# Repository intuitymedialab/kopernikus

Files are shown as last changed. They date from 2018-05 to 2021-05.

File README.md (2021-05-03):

# Kopernikus Documentation

*an experimental prototyping platform to test and evaluate the vision of home robotics*

Developed at Intuity Media Lab GmbH in Stuttgart, Germany.

Kopernikus Total

## 🤔 Wait, what?

For a high level overview of the project, visit [https://kopernikus.intuity.de/](https://kopernikus.intuity.de/).

## 🔬 What this is about

Kopernikus is a small robot, that will cost less than EUR 1000 to build. If you put it together, you will have something like a remote control car, equipped with a quad core computer, a stereo camera, audio input and output and a video projector.
You'll be able to use it as a basic setup and build your personal project on top.

## 📓 A little backstory

The vision of home robotics is ubiquitous. As a transdisciplinary team of designers, technologists and researchers, we were looking for a way to prototype the concepts we've been working on.

The question becomes: how do you design AI? How can we build behavioural interfaces? One common example is robot navigation.

We want future robots to navigate through our apartments savely, in a manner that is understandable and predictable for humans. We want them to deal gracefully with unexpected obstacles and be efficient and save. 

One of our key interests is Heuristic Problem Solving, which uses concepts from cognitive science to implement a decision process similar to that of humans (You can read up on HPS <a href="https://easychair.org/publications/open/z2d">here</a>, a Paper by our team member Alexandra Kirsch). Our goal is to use HPS as a general, cognitively inspired decision-making framework and use Kopernikus as a use case and testing environment to gain insights through practical experiences. 

That's why Kopernikus is an experimental prototyping platform to test and evaluate the vision of home robotics.

## 💪 What you will be able to do

Fully loaded, Kopernikus offers the following hardware capabilities:

* 3D imaging
* mobile projection mapping (up to a certain extent)
* 3 channel audio input (good for locating sound sources)
* audio playback
* mobile, untethered use for about an hour(...ish - depends on your use)

## 🎒 What you will need

**Quick disclaimer:** *One of our main goals was to build Kopernikus as both low-budget and easy-to-use as possible. At some points compromises had to be made in order to a) stay in a reasonable budget or b) make it easy to assemble and use.*

All of the components can be bought online on Amazon, eBay, Banggood, Mouser etc. - prices might vary.

This is just a rough rundown of what key components were used so you get the idea. Check out the [parts list](Hardware/partsList.md) for a more detailled list with links.

#### 💻 Computing
* UpBoard
* Arduino Uno

#### 👀 Input
* RealSense R200
* USB Microphones
* RC Receiver

#### 🐸 Output
* RD02 Robotic Drive System
* Servo Motor
* Anker Soundcore
* USB soundcard
* PicoPro Projector

#### ⚡️ Power
* Laptop Powerbank

### Custom Parts

In order to hold everything together we went with a round base plate (in size similar to vacuum cleaning robots) with some mounting holes in a grid and 3D printed parts made from PLA. We used an Ultimaker 3 - which means, you can basically print them on any basic FDM printer.

Most parts were designed with quite broad tolerances so you shouldn't have that big of a problem to make it all fit together nicely.

The shielding for the projector out of acrylic glass is optional - its mainly meant to protect the projector from dust and physical damage (and because we liked the look to be honest 😎). We will upload a 3D file without the mounts for it later.

## Getting started

For getting started head over to the specific readmes on [Software](Software/README.md) and [Hardware](Hardware/README.md).

## TODO

* [x] Prepare 3D files for milling
* [ ] Create schematic
* [x] Create 3D files for milling

## License

This project is released under the MIT License - you are free to do whatever you want with it - as long as you don't plan on subdueing humanity or any other crazy stuff, we're fine with it.

You are not legally bound to it, but it would be nice if you credit this project when creating something with it - and please **tell us**! We would love to see what you create!

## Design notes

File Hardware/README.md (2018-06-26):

# Kopernikus Software Documentation

*an experimental prototyping platform to test and evaluate the vision of home robotics*

Developed at Intuity Media Lab GmbH in Stuttgart, Germany.

## Overview

Let's divide this up into ~~two~~ three parts:
1) Parts list
2) Assembly
3) Connecting everything

## 🛠 Fabrication

As mentioned before, all parts can be either 3D-printed or produced on a laser cutter / CNC mill.

### 3D printed parts

The parts were printed on an Ultimaker 3 in our office, but any FDM printer should produce similar results.
The models were created for printing them directly onto the build plate with as little support as possible to create one even reference surface.
The layer height was 0.1mm on finer objects and 0.3mm on the rough stuff.

### Machined parts

We used 5mm PVC for our base plate and the controller plate. We wouldnt recommend going a lot thinner, but 4mm should be fine too.
Using acrylic glass instead of PVC shouldn't be a problem either, we just had it laying around already.

---

⚠️ **Especially when using a laser cutter, stay away from PVC since it creates toxic fumes when cut!** ⚠️

---

## 🔌 Connect all the things!

Refer to [this](components/basic_electronic_connections.pdf?raw=true) plan on how to connect everything. Fitting all wires into the plan would probably have been to big and unnecessary - it's actually quite simple.

The pin mappings on the Arduino are:

```
Pin mappings Arduino:

RC_CH1_INPUT     - >    5
RC_CH2_INPUT     - >    6
RC_CH3_INPUT     - >    7
RC_CH4_INPUT     - >    4 
SERVO PIN        - >   11
RX               - >   10
TX               - >    9
```

### Power

Basically everything runs off a notebook powerbank that has all the charging and protection features already built in - so no working on risky LiPo battery packs is required here.

The battery pack can deliver up to 50W peak which is more than enough for our use. One issue we had from time to time though was that the battery pack has a protection built in that shuts off the power when too little current is drawn. This totally makes sense when using it for its intended purpose (which we don't).

#### Adding a power resistor
At some point this problem somehow vanished, but one possible solution would be adding a **power resistor** that draws a fixed base current and thus circumvents the automatic shutdown. It also increases the power draw in general, but it's probably the simplest solution.

We still need to check what value would be a good match though. Open to suggestions.

#### Basic power scheme

We created two independent circuits so you can control which devices are powered to save some battery life.

1) Arduino, RC receiver, motors, servo
2) UpBoard and its peripherals (like the 3D camera, microphones etc.)

Ready-made devices like the speaker, the projector etc. get their juice directly via USB and all have a power switch themselves.

#### Powering the UpBoard

The UpBoard uses a simple DC jack, but **behold**!
Usually these are used for 9V and 12V which **you should never at any time** feed into the UpBoard. 

**! The UpBoard takes 5V MAXIMUM !**

Eventhough the powerbank has a 5V output, it can't deliver enough current for the UpBoard to boot properly. Thus we used a cheap step down buck converter, capable of delivering up to 12 A (not the small LM2596 ones), set to 5V.

We also added a decoupling capacitor across the 5V and GND rails on the board - not sure if it's necessary after all.

#### Powering the motors

This is pretty straight-forward: The motor drivers need 12V to work, so you can just connect them directly to the battery pack.

#### Powering the Arduino (and peripherals)

The Arduino gets its power from the MD25 Board's integrated voltage regulator. It's powerful enough to power the Arduino and the RC receiver, but peripherals like the Servo need their own supply (in form of a 5V 1A Step-Down Module)

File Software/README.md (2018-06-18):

# Kopernikus Software Documentation

*an experimental prototyping platform to test and evaluate the vision of home robotics*

Developed at Intuity Media Lab GmbH in Stuttgart, Germany.

## Overview

There are two software packages needed
1) Arduino
2) UpBoard

## 🤖 Arduino Code

The Arduino is used for everything hardware related. This includes:
* Controlling the motors and reading their encoder values
* Receiving RC commands
* Controlling the servo
* Talking to the UpBoard via a serial protocol

### Libraries

We rely on some libraries that you will need to install prior to flashing the Arduino:
* ServoTimer2
* CommandHandler
-> 
* EnableInterrupt
-> [GitHub Repo](https://github.com/GreyGnome/EnableInterrupt)
* AltSoftSerial

They are all available through the Libary Manager included in the Arduino IDE.

### Flashing the Arduino

Getting the Arduino ready should be pretty straight-forward:

1) Download the [Arduino IDE](https://www.arduino.cc/en/Main/Software)
2) Download our files
3) Install the necessary libraries
4) Choose the appropriate board settings
5) Upload 🚀

## 💻 UpBoard

The UpBoard is a x86 based single board computer, so we are able to run a fully-fledged Ubuntu distro on it and thus write code in all kinds of environments.

### Setup

Getting the UpBoard set up properly might be a bit finicky or at least different when you come from a background mainly working with Raspberry Pis. Some packages and kernel versions are not compatible with the latest Ubuntu so better stick with [Ubuntu 16.04 (Xenial Xerus)](http://releases.ubuntu.com/16.04/).

Also make sure you [install the kernel updates](https://wiki.up-community.org/Ubuntu#Install_Ubuntu_kernel_for_UP_from_PPA) for the board afterwards!

### Software packages

#### Ubuntu Software Packages

These packages can be installed via *apt* using the following commands:

```
sudo apt-get install "package name"

// so something like this:

sudo apt-get install git
```
* git, gitk, git-gui (Git)
* mplayer (Media Player)
* audacity (Audacity for recording sound)
* default-jre (Java)

The main software responsible for decision making is written in Clojure. Head over to the specific readMe for further documentation.

#### Camera

The camera supports ROS as the main interface. Therefore we use ROS to connect the camera to Clojure. It would be possible also to run the serial connection to the base over ROS, but since ROS can be such a pain, it seems better to use it only when necessary.

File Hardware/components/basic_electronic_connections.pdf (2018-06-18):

## microphones

12 V

kopernikus | // basic electronic connections

the arduino gets its
power from the voltage
regulator in the md25

the usb hub is mainly used for charging compatible devices like the bluetooth speaker eventough it has its own battery already.

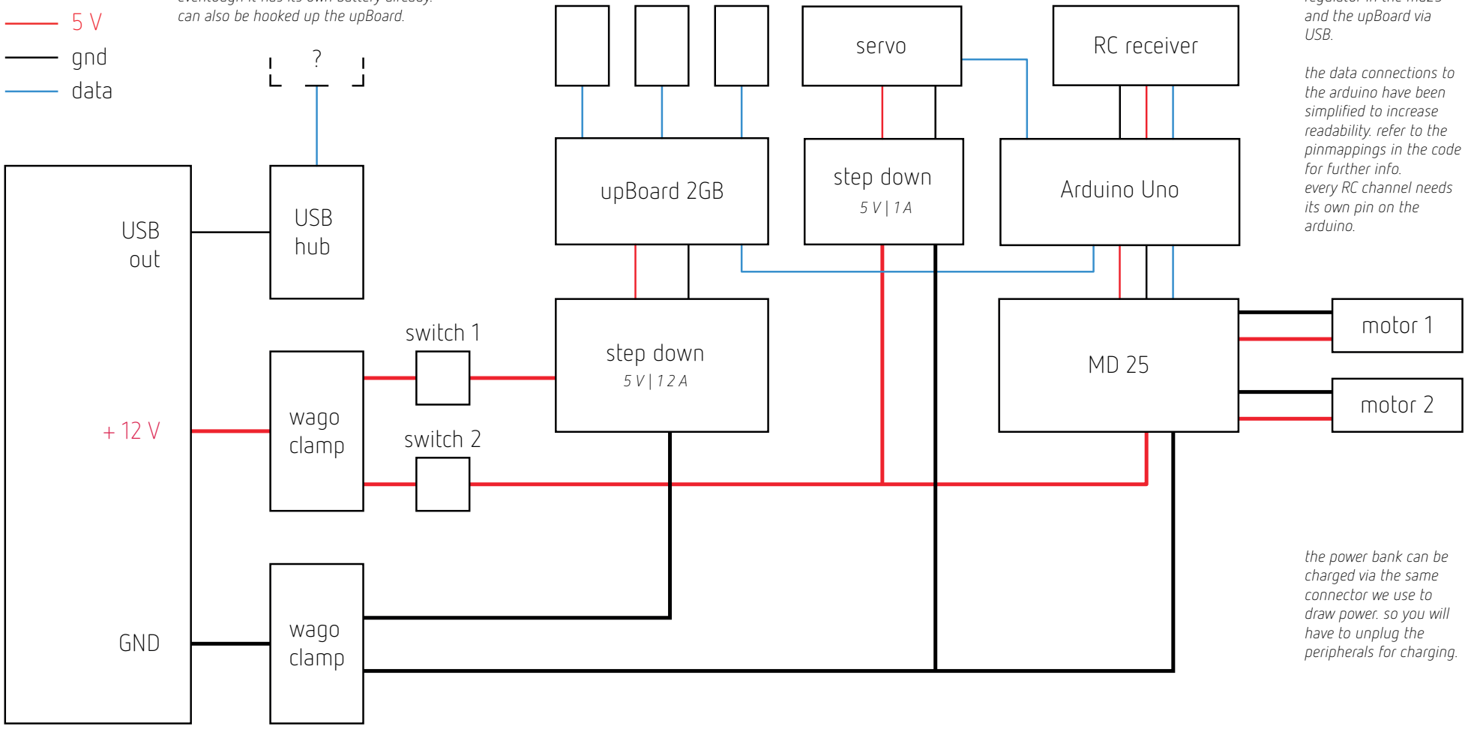
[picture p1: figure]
Arduino Uno; motor 1; motor 2; servo; RC receiver; step down 5 V | 1 A upBoard 2GB; step down; wago clamp; USB hub; 5 V gnd data; wago clamp GND; USB out; switch 1; switch 2; and the upBoard via USB.; the data connections to the arduino have been simplified to increase readability. refer to the pinmappings in the code for further info. every RC channel needs its own pin on the arduino.; the power bank can be charged via the same connector we use to draw power. so you will have to unplug the peripherals for charging.; can also be hooked up the upBoard. ?

intuity.de | aaiirr.net | kopernikus.bot | ⁄ª

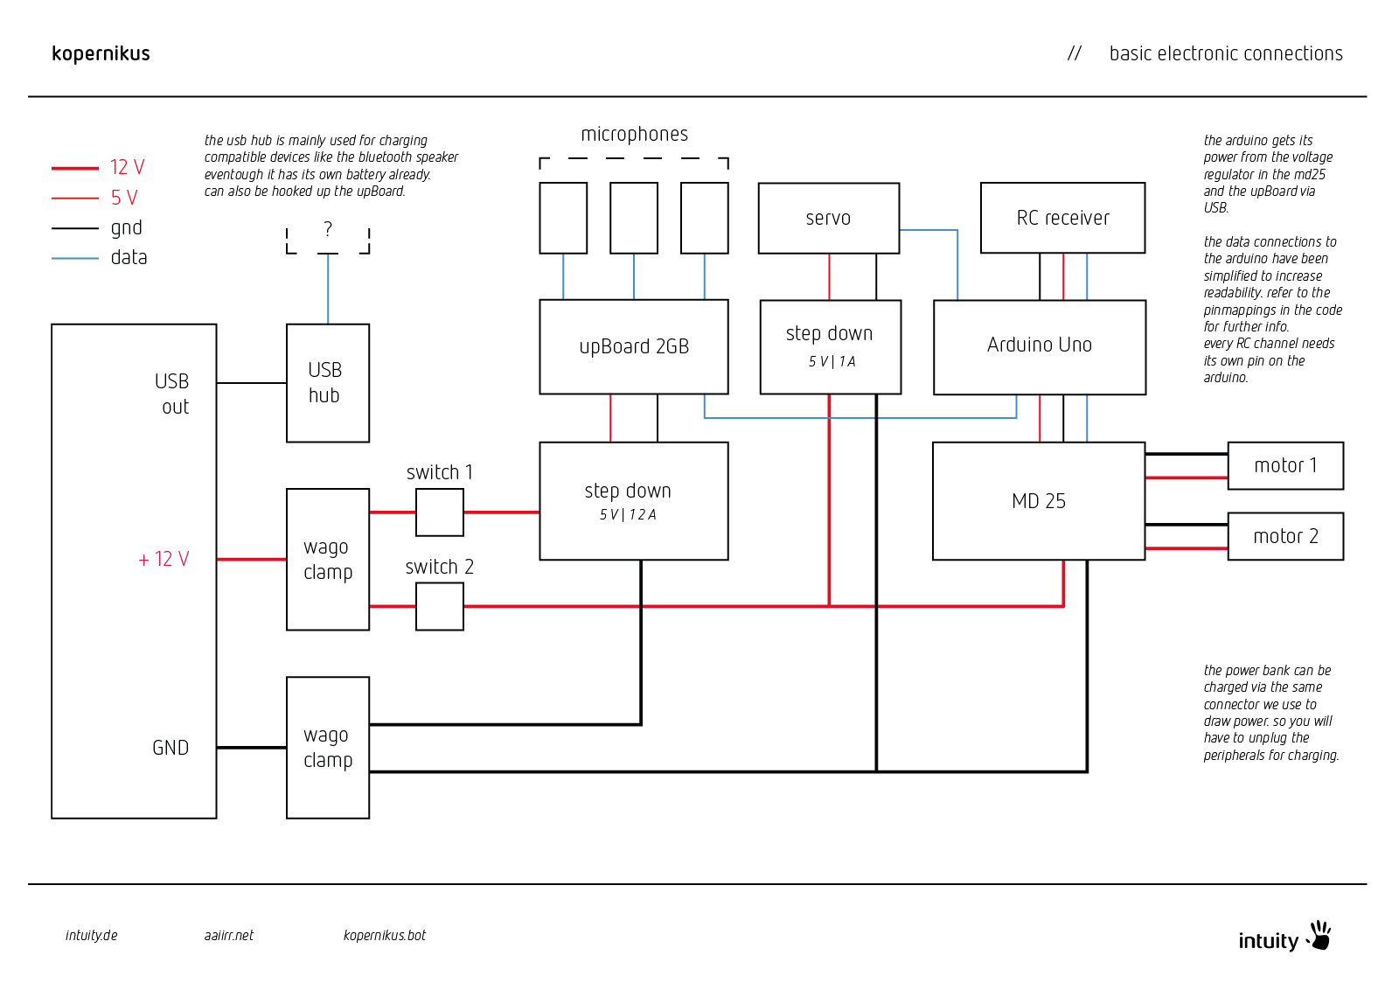
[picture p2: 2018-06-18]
Hardware/components/basic_electronic_connections.png

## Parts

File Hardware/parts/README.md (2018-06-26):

# Custom Parts

The 3D models were created with [Rhino 3D](https://www.rhino3d.com) - a commercial NURBS modelling software.

We uploaded both the NURBS and mesh-based models of Kopernikus, so you will be able to work with it.

## Download

-> NURBS (3dm format, zipped)

-> MESH (stl format, zipped)

## 3D Printing | Individual components

| parts count | name | filename |
| --- | --- | --- |
| 2 | Wheel Mount | motorwheel.stl |
| 2 | Omni Wheel Mount | omniwheel.stl |
| 2 | Controller Plate Mount | controllerplatemount.stl |
| 4 | Ring Mount 1 | ringmount_1.stl |
| 4 | Ring Mount 2 | ringmount_2.stl |
| 1 | Drum Mount Left | drummount_left.stl |
| 1 | Drum Mount Right | drummount_right.stl |
| 1 | Drum Left | drum_left.stl |
| 1 | Drum Right | drum_right.stl |
| 2 | Motor Hub 1 | motor_hub_1.stl |
| 2 | Motor Hub 2 | motor_hub_2.stl |
| 1 | USB Hub Mount 1 | usbhubmount_1.stl |
| 1 | USB Hub Mount 2 | usbhubmount_2.stl |
| 1 | Projector Mount Left | projectormount_right.stl |
| 1 | Projector Mount Right | projectormount_left.stl |
| 1 | RealSense Mount Left | realsensemount_left.stl |
| 1 | RealSense Mount Right | realsensemount_right.stl |
| 2 | RealSense Mounting Bracket | realsensemount_bracket.stl |

## Milling / Laser cutting | Individual components

| parts count | name | filename |
| --- | --- | --- |
| 1 | base plate | groundplate.stl |
| 1 | controller plate | controllerplate.stl |

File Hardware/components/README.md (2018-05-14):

# Parts List (DE)

These are all the main parts you will need for a replica of the robot.

This is a list for German buyers - the amazon products should be internationally available, but more specialized items might have to be ordered from other stores.

### Main components

#### 💻 Computing

* AAEON UpBoard 2 GB / 16 GB (x86 Chipset, Main Controller)
-> [mouser DE](https://www.mouser.de/ProductDetail/AAEON-UP/UP-CHT01-A12-0432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)

* UpBoard WiFi Dongle
-> [mouser DE](https://www2.mouser.com/ProductDetail/AAEON-UP/OPT-UP-WF-002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)

**Quick note** : *You might just want to get the [Intel RealSense Robotic Development Kit available at Mouser](https://www2.mouser.com/ProductDetail/Intel/82634DSRBTDVK?qs=33AqgSIO4a5twM1ZKUoNuA%3d%3d), which icludes the board and the RealSense camera.*

#### 👀 Input
* RealSense R200 (3D Camera) (*see above*)
* 3 x Mini USB Microphone -> [amazon](https://www.amazon.de/Mikrofon-Stecker-Sprachaufnahme-2-0Wireless-kleinste/dp/B01KWWYJA2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)
* FS-IA6 (Remote Control) -> [banggood](https://www.banggood.com/de/FlySky-FS-i6-2_4G-6CH-AFHDS-RC-Transmitter-With-FS-iA6B-Receiver-p-983537.html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)

#### 🐸 Output
* Anker Soundcore Mini (though any portable 'boom box' should do)
-> [amazon](https://www.amazon.de/Anker-SoundCore-Bluetooth-Lautsprecher-Reichweite-Schwarz/dp/B01HTH3C8S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)
* CSL External Soundcard
-> [amazon](https://www.amazon.de/CSL-Externe-Soundkarte-Virtual-Surround/dp/B00C7LXUDY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)
* PicoPro Projector *(sadly it has been discontinued, can still be bought used for quite cheap compared to its original price - any suggestions for a successor?)*

#### 🏃 Motion
* Arduino Uno R3
-> [arduino.cc](https://store.arduino.cc/arduino-uno-smd-rev3)
* Robot Electronics RD02 (12V Robot Drive System)
-> [EXP Tech](https://www.exp-tech.de/module/motorsteuerung/gleichstrommotoren/4318/rd02-12v-robot-drive-system)
* HD1810MG (Servo Motor)
-> [banggood](https://www.banggood.com/de/Power-HD-1810MG-3_9KG-High-Torque-Digital-Servo-for-450-Helicopter-p-1062442.html)
* 2 x Inline Skate wheels
-> 
* 2 x Omniwheels -> [krause robotics](http://krause-robotics.de/xtshop/Antriebe/Raeder/Allseitenraeder/Allseitenraeder-40-mm:::99_100_106_115.html)

#### ⚡️ Power
* XT Power 16000 mAh Powerbank incl. Charger
-> [amazon](https://www.amazon.de/XTPower®-XT-16000QC2-Powerbank-moderner-15600mAh/dp/B071L3QMCS/ref=sr_1_11?ie=UTF8&qid=1526297371&sr=8-11&keywords=notebook%2Bpowerbank&th=1)
* Step Down Module (12 A) 
-> [amazon](https://www.amazon.de/dp/B00HV4EPG8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)
* LM2596 Step Down Module (1 A)
-> [amazon](https://www.amazon.de/LM2596-DC-Wandler-Step-Down-Modul-1-5-35V/dp/B01H70Q5GI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)
* Anker USB Hub
-> [amazon](https://www.amazon.de/Anker-Datenhub-Ultrabooks-weiteren-kompatiblen/dp/B00Y211AFM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)

#### ⚙️ Other
* 3 x USB extension cable (about 0,5 m should be enough)
-> [amazon](https://www.amazon.de/dp/B00P0ES0VC/ref=sspa_dk_detail_4?psc=1)
* 3 x micro USB Cables
-> [amazon](https://www.amazon.de/Anker-PowerLine-Ladekabel-Lebensdauer-Smartphones-Schwarz/dp/B016BEVNK4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)
* HDMI Ribbon Cable (Mainly used in FPV applications)
-> [amazon](https://www.amazon.de/SCHWARZES-Standard-normal-Schnittstelle-blackmagic-Black/dp/B06XRGHFT7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)
* micro-USB 3.0 to Micro-USB 3.0 cable (might be a little hard to find)
-> [amazon](https://www.amazon.de/gp/product/B00IJWHOK0/ref=oh_aui_detailpage_o04_s00?ie=UTF8&psc=1)
* 2 x switch
-> [amazon](https://www.amazon.de/OFF-Position-Snap-Wippschalter-schwarz/dp/B00WJLF8OQ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)
* 2 x WAGO 5-conductor splice connectors (NO. 221-415)
-> [amazon](https://www.amazon.de/Wago-221-415-Verbindungsklemme-5-Leiter-Betätigungshebel/dp/B0107SYYGU/ref=pd_lpo_vtph_328_tr_t_2?_encoding=UTF8&psc=1&refRID=AVA2H8VJZVBR0DRDD52C)
* DC Jack (5,5 x 2,1 mm)
-> [amazon](https://www.amazon.de/Liwinting-Verbinder-LED-Streifen-Licht-LED-Band-Licht-CCTV-Kamera/dp/B074GTKXWR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)
* some 12 AWG wire
* some jumper wires and pin headers
* some thin cable ties

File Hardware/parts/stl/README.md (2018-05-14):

# STL files

All the parts were created and exported with **Rhino 5**.

---> [DOWNLOAD](kopernikus_STL.zip?raw=true) <---

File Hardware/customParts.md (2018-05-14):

# Custom Parts

| parts count | Name | Filename |
| --- | --- | --- |
| 2 | Wheel Mount | 170920_motorwheel.stl |
| 2 | Omni Wheel Mount | 170920_omniwheel.stl |
| 2 | Controller Plate Mount | 170920_controllerplatemount.stl |
| 4 | Ring Mount 1 | 170920_ringmount_1.stl |
| 4 | Ring Mount 2 | 170920_ringmount_2.stl |
| 1 | Drum Mount Left | 170920_drummount_left.stl |
| 1 | Drum Mount Right | 170920_drummount_right.stl |
| 1 | Drum Left | 170920_drum_left.stl |
| 1 | Drum Right | 170920_drum_right.stl |
| 2 | Motor Hub 1 | 170920_motor_hub_1.stl |
| 2 | Motor Hub 2 | 170920_motor_hub_2.stl |
| 1 | USB Hub Mount 1 | 170920_usbhubmount_1.stl |
| 1 | USB Hub Mount 2 | 170920_usbhubmount_2.stl |
| 1 | Projector Mount Left | 170920_projectormount_right.stl |
| 1 | Projector Mount Right | 170920_projectormount_left.stl |
| 1 | RealSense Mount Left | 170920_realsensemount_left.stl |
| 1 | RealSense Mount Right | 170920_realsensemount_right.stl |
| 2 | RealSense Mounting Bracket | 170920_realsensemount_bracket.stl |

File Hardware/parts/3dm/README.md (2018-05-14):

# Rhino model files

All the parts were created with **Rhino 5**.

---> [DOWNLOAD](kopernikus_3dm.zip?raw=true) <---

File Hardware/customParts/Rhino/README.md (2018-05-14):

# Rhino model files

All the parts were created with **Rhino 5**.

---> [DOWNLOAD](kopernikus_3dm.zip) <---

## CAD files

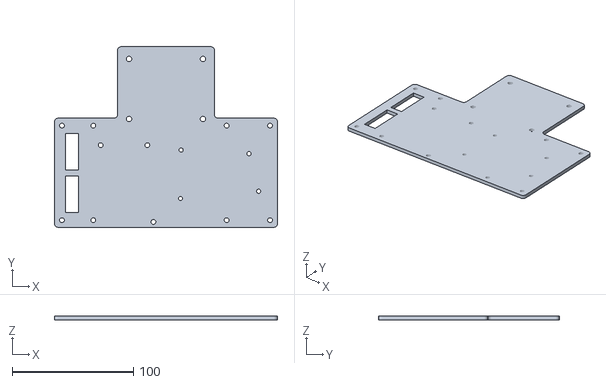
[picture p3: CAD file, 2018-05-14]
Hardware/parts/stl/_individualParts(cut)/controllerplate.stl
184.0 x 149.0 x 3.00

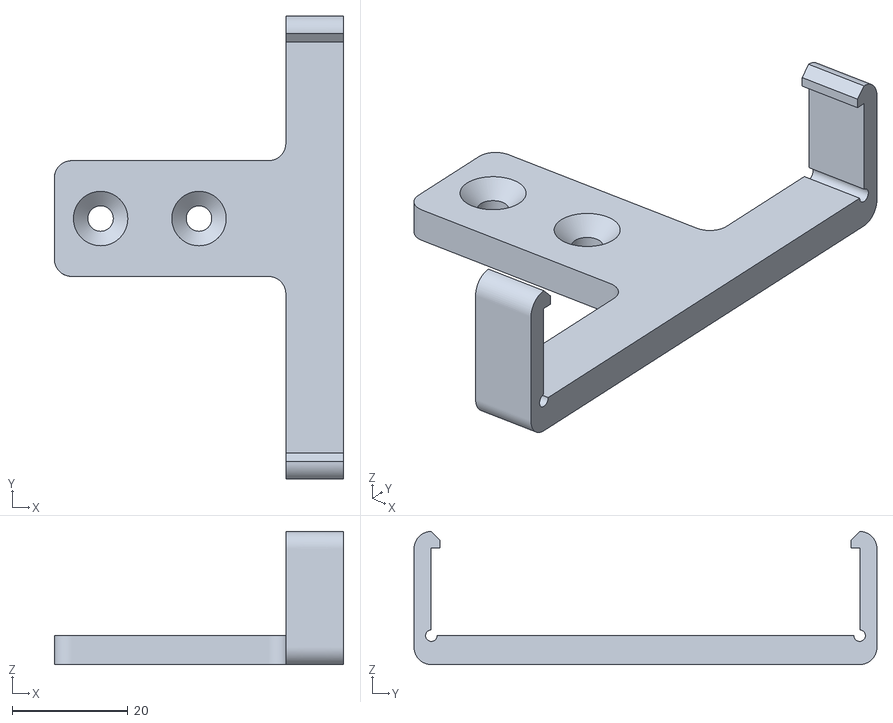
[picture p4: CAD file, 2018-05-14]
Hardware/parts/stl/_individualParts(print)/projector_mount_1.stl
50.0 x 80.0 x 23.0

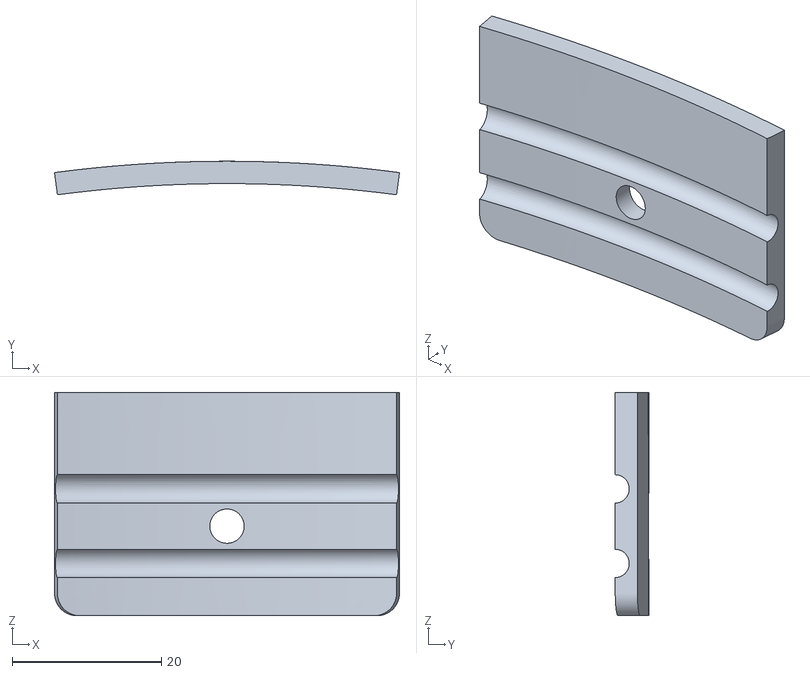
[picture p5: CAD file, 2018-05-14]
Hardware/parts/stl/_individualParts(print)/ubs_hub_mount_1.stl
46.3 x 4.50 x 29.9

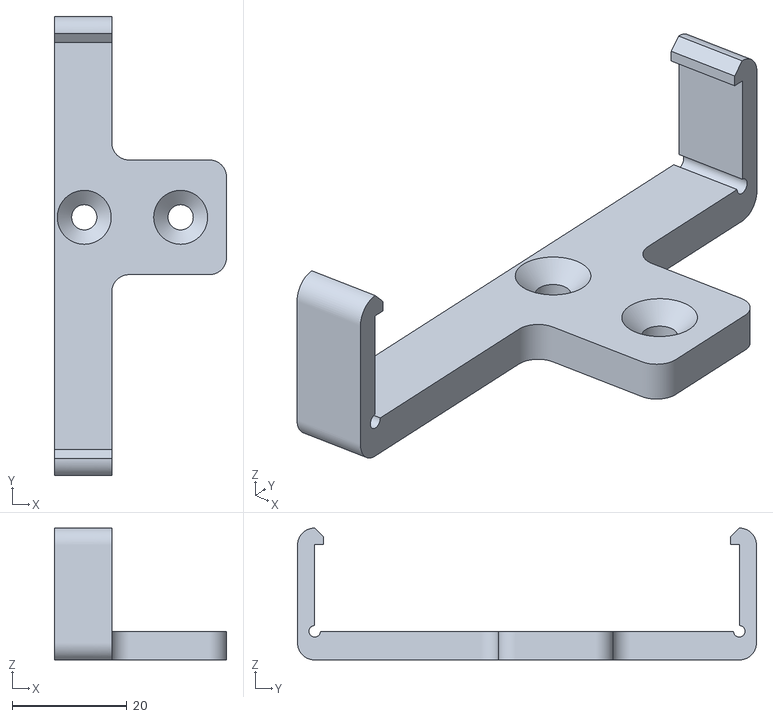
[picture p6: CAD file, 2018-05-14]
Hardware/parts/stl/_individualParts(print)/projector_mount_2.stl
30.0 x 80.0 x 23.0

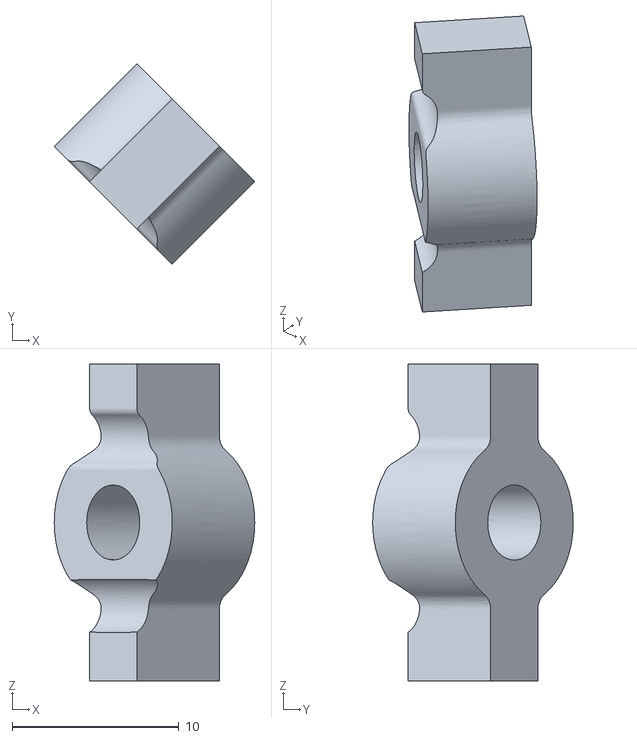
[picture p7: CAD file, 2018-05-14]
Hardware/parts/stl/_individualParts(print)/ring_mount_2.stl
12.0 x 12.0 x 19.0

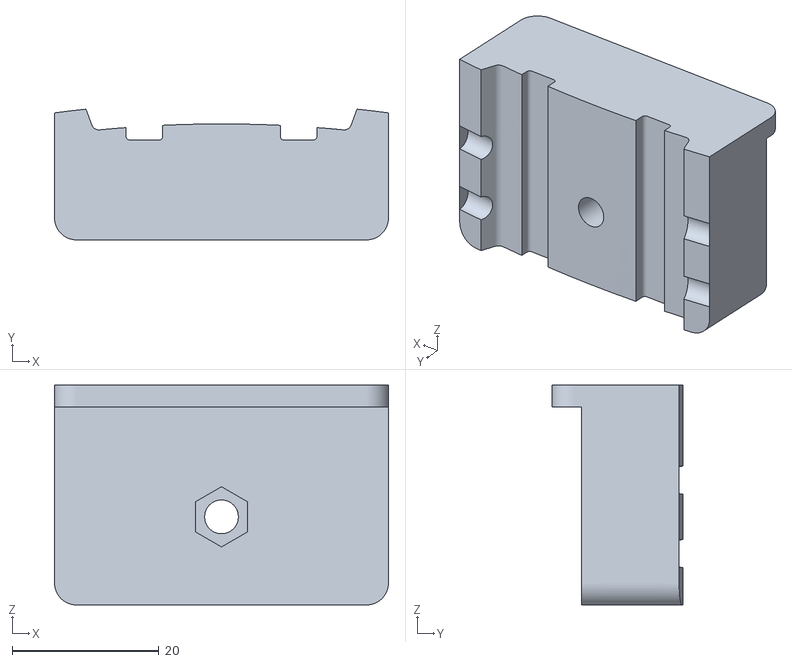
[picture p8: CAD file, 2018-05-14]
Hardware/parts/stl/_individualParts(print)/ubs_hub_mount_2.stl
45.5 x 17.8 x 29.9

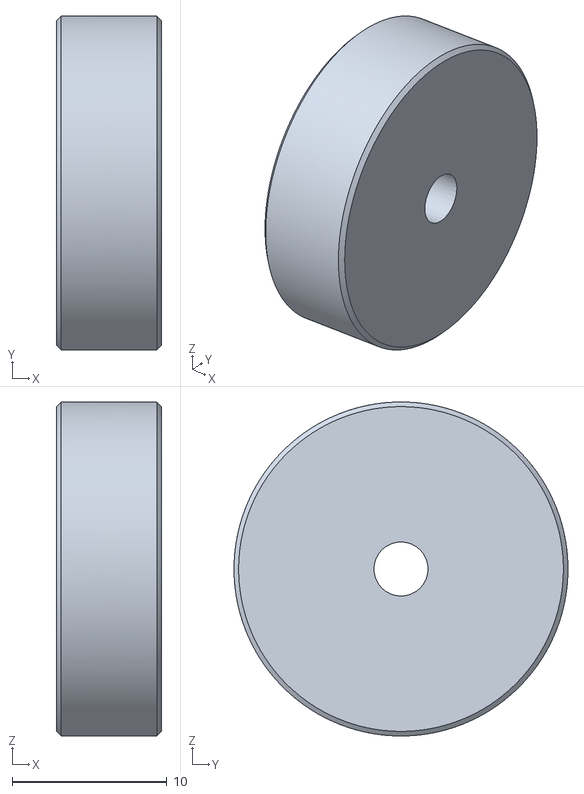
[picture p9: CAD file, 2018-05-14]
Hardware/parts/stl/_individualParts(print)/wheel_hub_1.stl
6.80 x 21.6 x 21.6

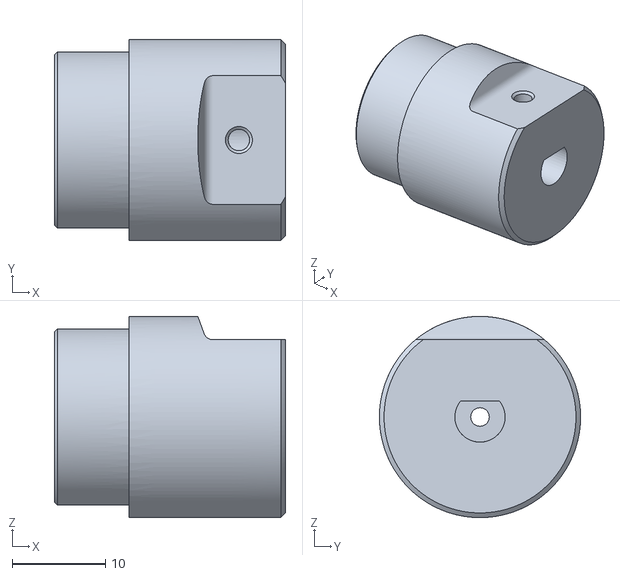
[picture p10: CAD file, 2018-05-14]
Hardware/parts/stl/_individualParts(print)/wheel_hub_2.stl
24.8 x 21.6 x 21.6

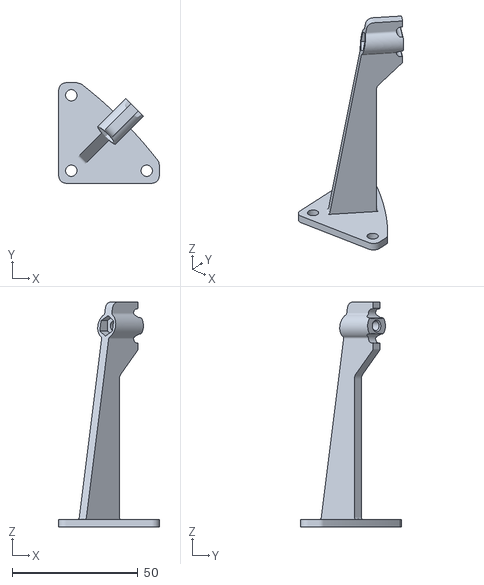
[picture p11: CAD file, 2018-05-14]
Hardware/parts/stl/_individualParts(print)/ring_mount_1.stl
40.0 x 40.0 x 89.5

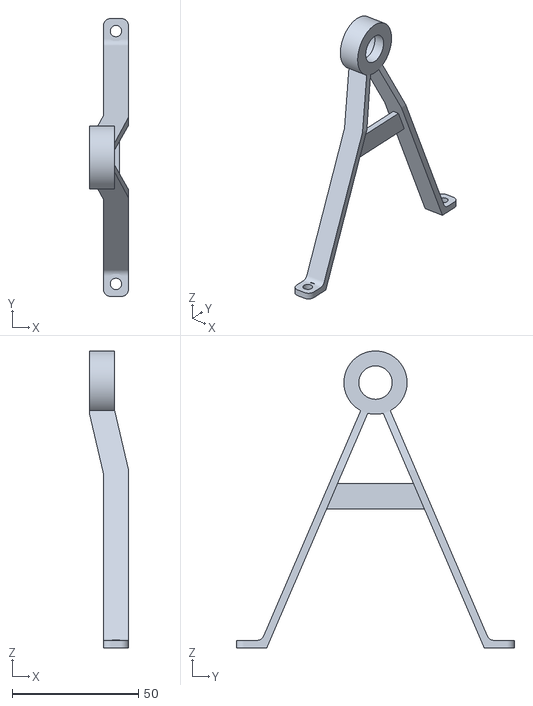
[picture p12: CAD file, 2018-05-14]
Hardware/parts/stl/_individualParts(print)/drum_mount_1.stl
15.5 x 110.0 x 117.5

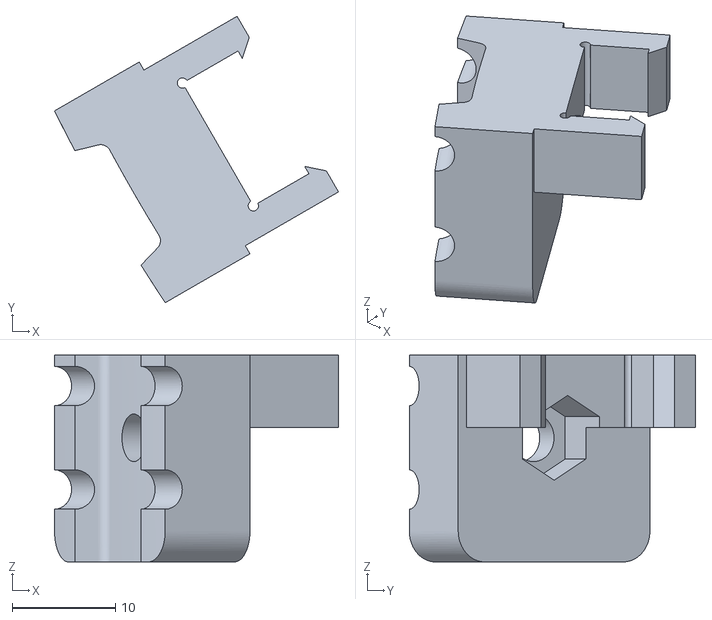
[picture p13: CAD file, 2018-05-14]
Hardware/parts/stl/_individualParts(print)/mic_mount_1.stl
27.4 x 27.7 x 20.0

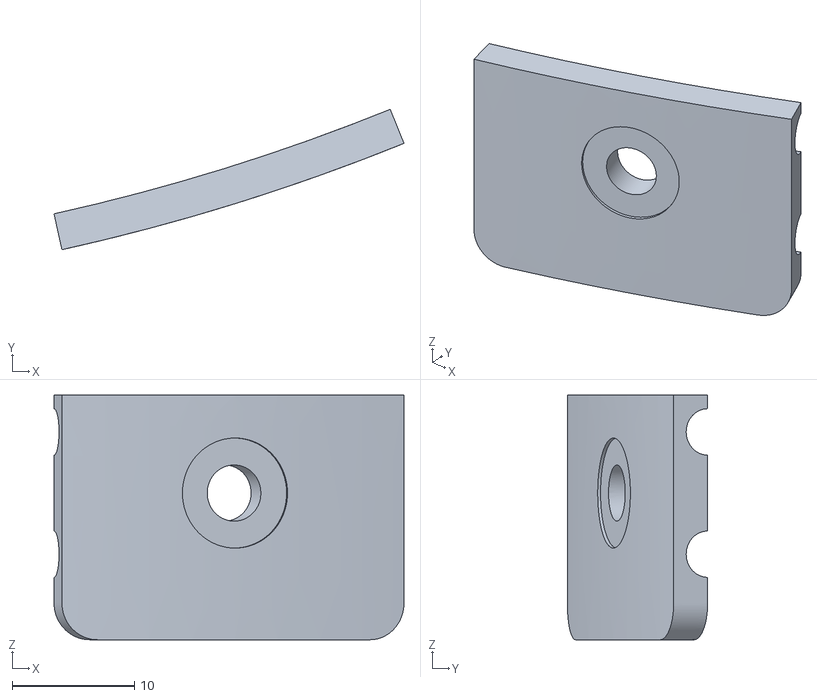
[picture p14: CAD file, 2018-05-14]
Hardware/parts/stl/_individualParts(print)/realsense_mount_1.stl
28.6 x 11.5 x 20.0

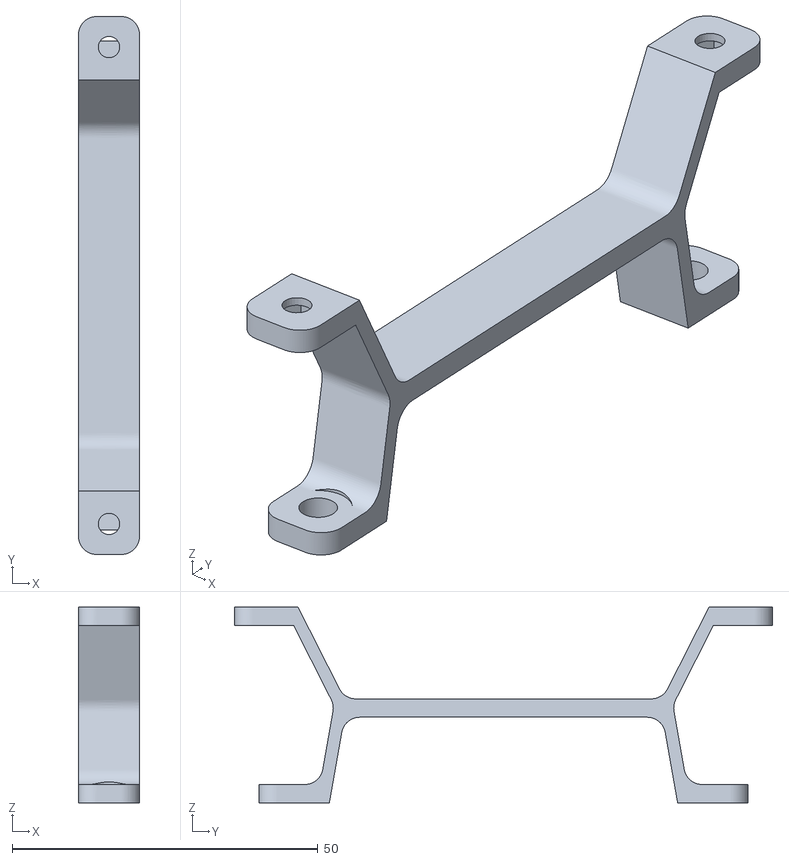
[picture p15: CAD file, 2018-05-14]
Hardware/parts/stl/_individualParts(print)/controller_plate_mount.stl
10.0 x 88.0 x 32.0

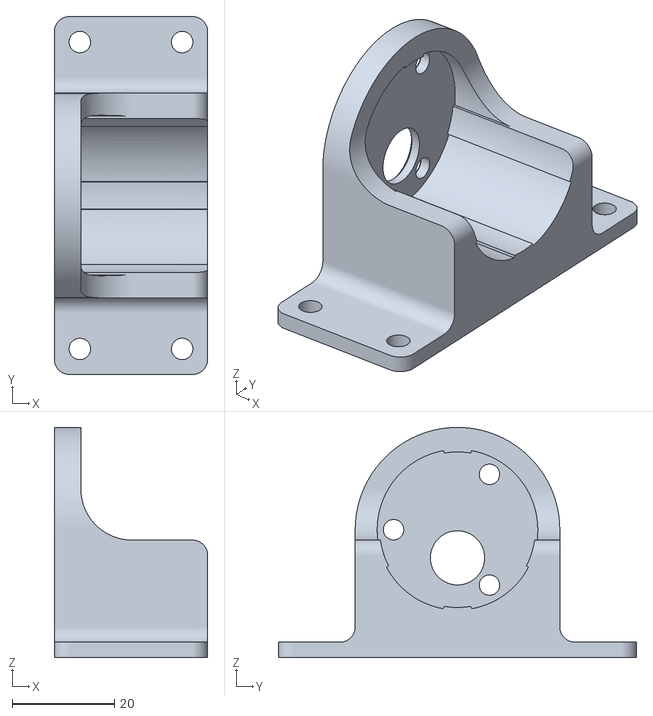
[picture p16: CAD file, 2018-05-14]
Hardware/parts/stl/_individualParts(print)/motor_mount.stl
30.0 x 70.0 x 45.0

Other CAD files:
Hardware/parts/stl/_individualParts(print)/drum_side_1.stl
Hardware/parts/stl/_individualParts(print)/realsense_mount_2_1.stl
Hardware/parts/stl/_individualParts(print)/mic_mount_2.stl
Hardware/parts/stl/_individualParts(print)/drum_mount_2.stl
Hardware/parts/stl/_individualParts(print)/omni_wheel_mount.stl
Hardware/parts/stl/_individualParts(print)/realsense_mount_2_2.stl

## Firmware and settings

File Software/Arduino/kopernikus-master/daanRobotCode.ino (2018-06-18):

////////////////////////////////////////////////////////////////////////////////////

#include <ServoTimer2.h>
#include <CommandHandler.h>
#include <EnableInterrupt.h>
#include <AltSoftSerial.h>

////////////////////////////////////////////////////////////////////////////////////

// PWM Pin for projector

#define PROJECTORPIN     11

// The projector servo is handled by Timer 2 to avoid jitter
ServoTimer2 projector;

unsigned long lastProjectorTime;
int projectorTarget = 90;
int projectorPos = 90;
int projectorDeltaTime = 10;

////////////////////////////////////////////////////////////////////////////////////

// MD 25 (Motor driver)

#define CMD        (byte)0x00            // MD49 command address of 0                                 
#define GET_VER          0x29
#define GET_ENC1         0x23
#define GET_ENC2         0x24
#define GET_VI           0x2C
#define GET_ERROR        0x2D
#define SET_ACCEL        0x33
#define SET_SPEED1       0x31
#define SET_SPEED2       0x32
#define SET_MODE         0x34
#define RESET_ENC        0x35

byte bat_volt, mot1_cur, mot2_cur = 0;
byte ver = 0;
byte error = 0;
float vel_l, vel_r;

long enc1 = 0;
long enc2 = 0;

////////////////////////////////////////////////////////////////////////////////////

// RC REMOTE

// Pins for receiving remote control commands
#define RC_NUM_CHANNELS  4

// channels:
// 1 - right stick vertical -> speed
// 2 - right potentiometer -> speed scale
// 3 - left stick horizontal -> turn
// 4 - left potentiometer -> projector

#define RC_CH1  0
#define RC_CH2  1
#define RC_CH3  2
#define RC_CH4  3

#define RC_CH1_INPUT  5
#define RC_CH2_INPUT  6
#define RC_CH3_INPUT  7
#define RC_CH4_INPUT  4


uint16_t rc_values[RC_NUM_CHANNELS];
uint32_t rc_start[RC_NUM_CHANNELS];
volatile uint16_t rc_shared[RC_NUM_CHANNELS];

// used to track whether remote has been used before in this session
boolean remoteOn = false;
unsigned long rcLastTime;

////////////////////////////////////////////////////////////////////////////////////

CommandHandler<> SerialCommandHandler;
AltSoftSerial softSerial;

////////////////////////////////////////////////////////////////////////////////////

void setup() {

  // USB connection
  Serial.begin(38400);
  SerialCommandHandler.AddCommand(F("setAccel"), setAccel);
  SerialCommandHandler.AddCommand(F("setVel1"), setVel1);
  SerialCommandHandler.AddCommand(F("setVel2"), setVel2);
  SerialCommandHandler.AddCommand(F("getEnc1"), getEnc1);
  SerialCommandHandler.AddCommand(F("getEnc2"), getEnc2);
  SerialCommandHandler.AddCommand(F("stopMotors"), stopMotors);
  SerialCommandHandler.AddCommand(F("setProj"), moveProjector);
  SerialCommandHandler.AddCommand(F("rstEnc"), resetEnc);

  // Connection to MD25 (Pins 8 & 9)
  softSerial.begin(19200);
  softSerial.write(RESET_ENC);
  cleanSoftSerial();

  // Inputs from remote control
  pinMode(RC_CH1_INPUT, INPUT);
  pinMode(RC_CH2_INPUT, INPUT);
  pinMode(RC_CH3_INPUT, INPUT);
  pinMode(RC_CH4_INPUT, INPUT);

  enableInterrupt(RC_CH1_INPUT, calc_ch1, CHANGE);
  enableInterrupt(RC_CH2_INPUT, calc_ch2, CHANGE);
  enableInterrupt(RC_CH3_INPUT, calc_ch3, CHANGE);
  enableInterrupt(RC_CH4_INPUT, calc_ch4, CHANGE);

  // Initialize and reset projector (center position)
  pinMode(PROJECTORPIN, OUTPUT);
  projector.attach(PROJECTORPIN);
  projector.write(calcProjectorDegree(projectorPos));

  // Reset timers
  lastProjectorTime = millis();
  rcLastTime = millis();

  Serial.println("Ready");
  Serial.println("Waiting for commands...");
}

void loop() {
  SerialCommandHandler.Process();

  if (rcLastTime + 200 < millis()) {
    rcLastTime = millis();
    rc_read_values();
    if (rcValid()) {
      Serial.println("valid");
      if (!remoteOn) {
        remoteOn = true;
        Serial.println("Remote control connected - disabling Serial control");
        remoteOn = true;
        mdSetDriveMode(2);
      }
      processRemote();
      Serial.println(rc_values[RC_CH1]);
      Serial.println(rc_values[RC_CH2]);
      Serial.println(rc_values[RC_CH3]);
      Serial.println(rc_values[RC_CH4]);
      Serial.println("---");
      resetRcValues();
    }
    else if (remoteOn) {
      remoteOn = false;
      mdSetDriveMode(0);
      Serial.println("Remote control disconnected - enabling Serial control");
    }
  }

  if (projectorPos != projectorTarget) {

    if (lastProjectorTime + projectorDeltaTime < millis()) {
      lastProjectorTime = millis();

      if (projectorPos < projectorTarget) {
        projectorPos++;
      }
      else {
        projectorPos--;
      }
      Serial.println(projectorPos);
      projector.write(calcProjectorDegree(projectorPos));
    }
  }
}

////////////////////////////////////////////////////////////////////////////////////

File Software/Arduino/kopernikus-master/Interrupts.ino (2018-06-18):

////////////////////////////////////////////////////////////////////////////////////

// Interrupt handling

void calc_ch1() {
  calc_input(RC_CH1, RC_CH1_INPUT);
}
void calc_ch2() {
  calc_input(RC_CH2, RC_CH2_INPUT);
}
void calc_ch3() {
  calc_input(RC_CH3, RC_CH3_INPUT);
}
void calc_ch4() {
  calc_input(RC_CH4, RC_CH4_INPUT);
}



void rc_read_values() {
  noInterrupts();
  memcpy(rc_values, (const void *)rc_shared, sizeof(rc_shared));
  interrupts();
}

void calc_input(uint8_t channel, uint8_t input_pin) {
  if (digitalRead(input_pin) == HIGH) {
    rc_start[channel] = micros();
  } else {
    uint16_t rc_compare = (uint16_t)(micros() - rc_start[channel]);
    rc_shared[channel] = rc_compare;
  }
}

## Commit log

2018-05-14 updated file names
    [controller_plate_mount.stl, controllerplate.stl, drum_mount_1.stl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]
2021-05-03 Update README.md
    Changed link to new domain https://kopernikus.intuity.de/
2021-05-03 Update README.md
    Fixed link text to new domain https://kopernikus.intuity.de/
